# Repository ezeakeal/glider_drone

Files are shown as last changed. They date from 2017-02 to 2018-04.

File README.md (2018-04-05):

# glider_drone

A project to send a drone/glider to the stratosphere, and get it back!

## Recomendations

Setup remote debug (https://nathanpjones.com/2016/02/remote-debug-gpio-on-raspberry-pi/)

# Required hardware

1. Balloon (Hwoyee HY-1000) http://randomaerospace.com/Random_Aerospace/Balloons.html
2. Parachute (18 in. Spherachute + 42 in. Spherachute) http://spherachutes.com/
3. Glider (Go Discover FPV EPO) https://hobbyking.com/en_us/hobbykingr-tm-go-discover-fpv-plane-epo-1600mm-kit.html
4. 2 LoRa radios (http://www.hoperf.com/rf_transceiver/lora/RFM95W.html) with some interface.
5. Raspberry Pi B 2
6. Raspberry Pi servo hat + sensor hats
7. LiIon battery packs (10000 mAh recommended.. I have 2)
8. GoPro or equivalent (Xiaomi Yi is pretty great)
9. Wide angle Raspberry Pi Camera (reverse view)
10. A BUNCH of Micro SD cards + USB storage for logging and PiCamera storage 

# Prerequisites

## Setup I2C

https://learn.adafruit.com/adafruits-raspberry-pi-lesson-4-gpio-setup/configuring-i2c

## Setup Raspberry Pi interfaces

Using `raspi-config` (https://learn.sparkfun.com/tutorials/raspberry-pi-spi-and-i2c-tutorial):
1. Enable I2C
2. Enable Camera
3. Enable Remote GPIO (optional - enabling now just in case I use it later)

## Setup the disks

The glider will record video and logs to a directory specified in `glider_conf.ini`
For example, images/videos will be written to `/data/camera' by default.
Make any required directories before execution (I recommend using a USB stick)

## Setup RTIMULib

Use the following RTIMULib and guide: https://github.com/RPi-Distro/RTIMULib/tree/master/Linux
You may need to adjust the sensor ID: https://simplifyrobotics.wordpress.com/2017/05/25/mpu9250-wrong-id-error/

## Calibrate the MPU

https://github.com/RPi-Distro/RTIMULib/blob/master/Calibration.pdf

Follow all the instructions for callibration (run RTIMULibCal inside of RTEllipsoidFit)
This will generate an RTIMULib.ini config file - move that to a well-known path.
Finally, set the full path to the RTIMULib.ini file in glider_conf.ini

## Setup the Servo Hat

https://learn.adafruit.com/adafruit-16-channel-pwm-servo-hat-for-raspberry-pi/library-reference

## Find the range of your servos

The min/max duty cycle of the servo pulse can be configured in the settings.

**Note:** It took me some trial and error to figure this out (read Weird things below)

Using the PWM controller library from Adafruit or geekroo, start sending pulses to your servo.
I did the following

```
from Adafruit_PWM_Servo_Driver import PWM
import time
pwm = PWM(0x70) # i2c address for the servo hat controller
pwm.setPWMFreq(50)

# Try find min/max angle values
# pwm.setPWM(0,0, int(4096/20*(pulse_fraction)))
# I decreased the value of pulse_fraction from 1, to 0.7 until the servo stopped moving
# Then I increased the value until it stopped moving the other way
# The command is setting the pulse duration (in multiples of 1ms out of 20ms pulse)
# So pulse_fraction = 1 means 1ms@5V, then 19ms@0V

# The min I found
pwm.setPWM(0,0, int(4096/20*(0.7)))
# The max I found
pwm.setPWM(0,0, int(4096/20*(2.6)))
```

Once you have these values, set them in glider_conf.ini

### Weird things that happened

When I was trying to test the servos, some weird things happened before I found the range.

* Servo was sweeping through 30 or 40 degrees when I tried setting a new pulse width.
    * Not like a jitter or twitch, this was random sweeping for a few fractions of a second each time.
    * I thought that the servo was broken or frequency was wrong.
    * They were bad assumptions. Turns out that doubling the frequency reduced the symptom
        * Initial pulse was now reasonable in some cases!
        * But a second pulse was being sent, causing weirdness.
* Generally: if a pulse is 20ms long (50hz frequency), then:
    * 2ms high (5V) + 18ms low represents 180deg
    * 1ms high represents 0deg
* I was setting some mad values outside of this range
    * The library takes a the pulse width as a portion of 4096 (e.g. 1024 is 25% pulse width)
* **Important:** IF you give the servo a terrible value, it may not recover from trying to reach that, and future values may not work.
    * This is what led to such confusion on my part. I was putting the servo into a weird state because I lacked prior knowledge on servo pulses.

# Internal notes

## Features:
    Homesickness routine:
        If no signal from groundstation received, do not disengage from balloon
        Probably send a flag (trust of glider behaviour = True/False)
            So during flight, you flick that switch in groundstation
    Dual antennas:
        Two orientations during flight (vertical, and gliding)
        So two antennas
    IMU mounted away from electronics
    LEDs for status:
        Help Debug whats going on (issue was disk mounting this time)
    Shielded servo lines
    SMS also
    Directional tracker
    Return to sender information (like who the fuck I am)
    Better FSTAB control - must mount everytime!

## Nice to have:
    Smoke trails
    Fireworks
    Loud beeper for finding
    Groundstation application which shows where the satellites are with overlay on camera!



## Todo list:
    Fix the GPS tracking in the IMU module
        GPS tracking set the offset for the IMU, but tracking was degrees, IMU was radians

## Flight tests:
    Shake test
    Radar test (ticknock to elsewhere)
    Parachute test

newline

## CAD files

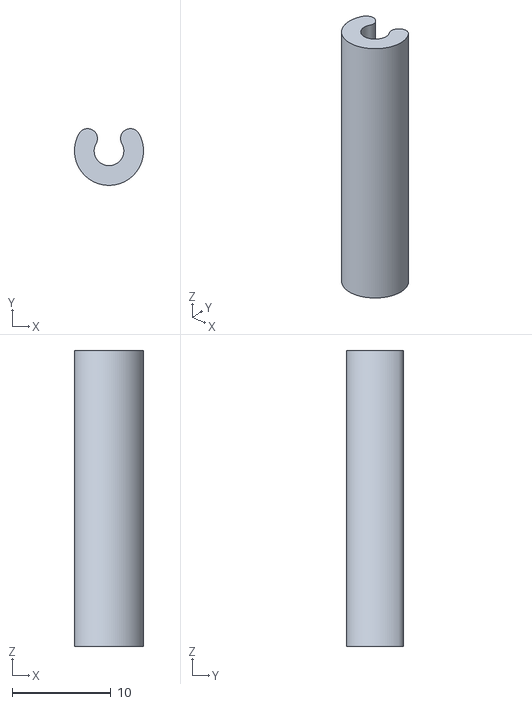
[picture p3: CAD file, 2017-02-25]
resources/3D Printed Parts/dipoleclip.stl
7.00 x 5.75 x 30.0

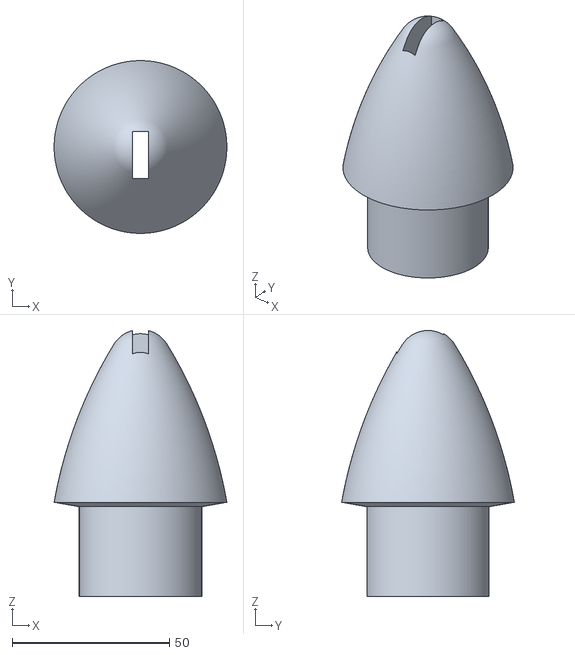
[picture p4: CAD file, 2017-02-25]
resources/3D Printed Parts/tailcone.stl
55.0 x 55.0 x 84.7

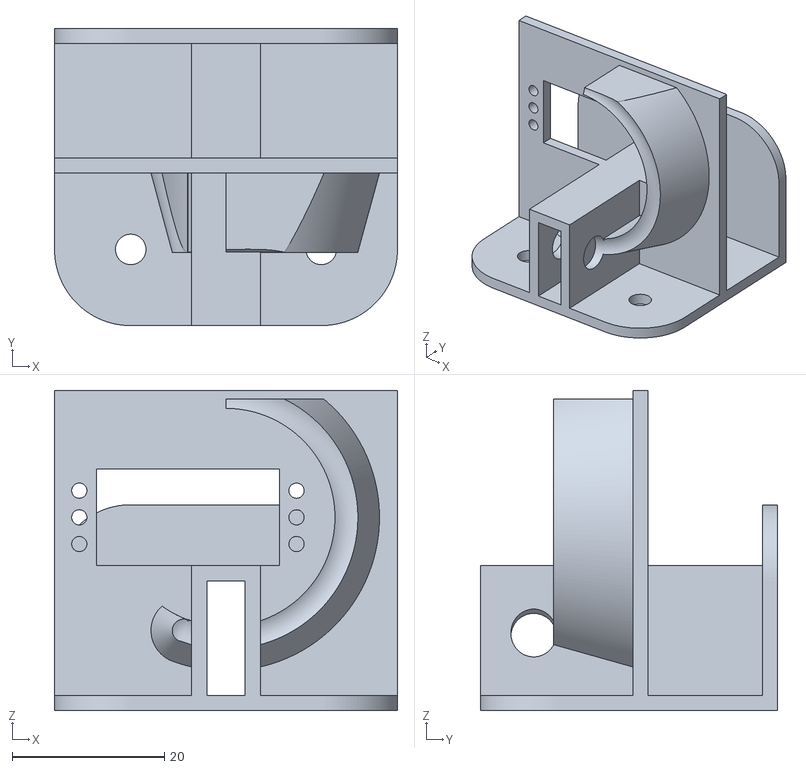
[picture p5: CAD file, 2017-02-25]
resources/3D Printed Parts/releasebracket.stl
45.0 x 39.0 x 42.0

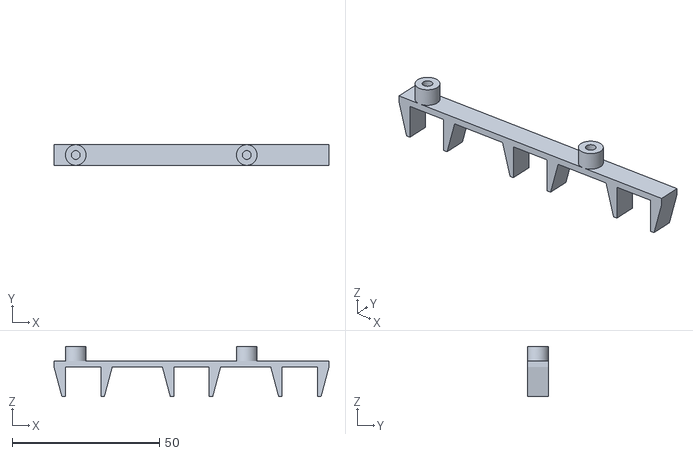
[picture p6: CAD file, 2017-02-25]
resources/3D Printed Parts/piholder.stl
93.3 x 7.00 x 17.0

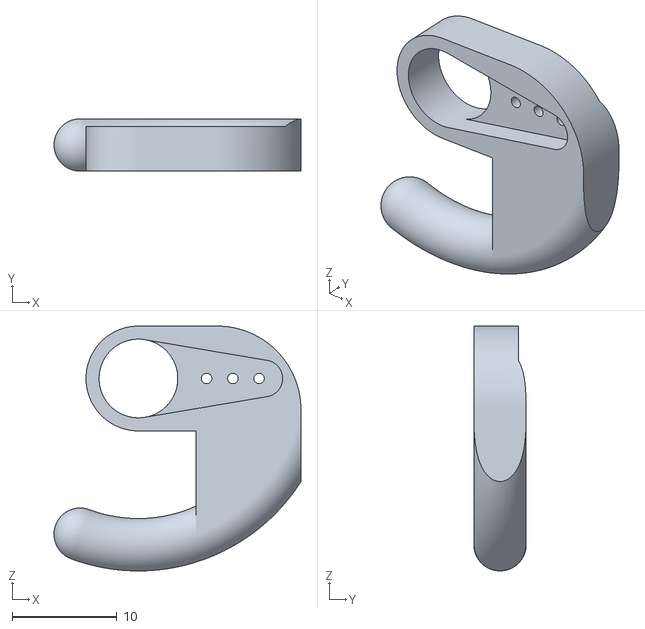
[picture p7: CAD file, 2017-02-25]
resources/3D Printed Parts/releasehook.stl
23.6 x 5.00 x 23.3

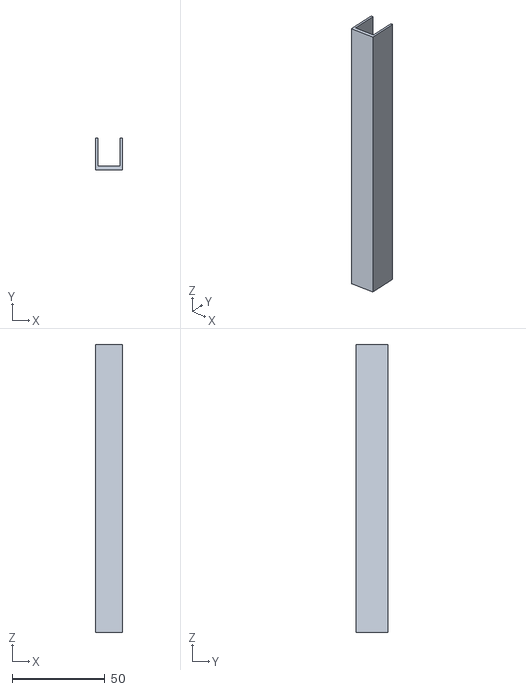
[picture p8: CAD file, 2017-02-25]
resources/3D Printed Parts/channel.stl
14.4 x 17.0 x 155.0

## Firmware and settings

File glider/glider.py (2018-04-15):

import glob
import os
import logging
import logging.config
import subprocess
import traceback

##########################################
# Configure logging
##########################################
base_dir = os.path.dirname(__file__)
conf_path = os.path.join(base_dir, "glider_conf.ini")
logging.config.fileConfig(conf_path)

LOG = logging.getLogger("glider")
logging.getLogger("Adafruit_I2C").setLevel(logging.WARN)

#########################################
# Import glider modules and states
#########################################
from modules.glider_gps import GPS
from modules.glider_camera import GliderCamera
from modules.glider_imu import IMU
from modules.glider_pilot import Pilot
from modules.glider_pwm_controller import GliderPWMController
from modules.glider_radio import GliderRadio
from modules.glider_telem import TelemetryHandler

import glider_states as gstates


##########################################
# MAIN
##########################################
class GliderCommandMixin(object):
    COMMAND_DIRECTIVES = None
    commands_received = 0
    last_command_dir = ""

    def setup_command_directives(self):
        self.COMMAND_DIRECTIVES = {
            "PA": self.pitch_change,
            "O": self.state_change,
            "TS": self.turn_severity_change,
            "DEST": self.destination_change,
            "IMAGE": self.image_command,
        }

    def command_handler(self, msg_dict, **kwargs):
        LOG.info("Handling command: %s %s" % (msg_dict, kwargs))
        command_data = str(msg_dict['message'])
        command_parts = command_data.split("|")
        command_instruction = command_parts[0]
        command_function = self.COMMAND_DIRECTIVES.get(command_instruction)
        if not command_function:
            LOG.error("No command found for instruction: %s" % command_instruction)
            return None
        try:
            self.commands_received += 1
            self.last_command_dir = command_instruction
            return command_function(command_parts)
        except:
            LOG.exception("Error in running command")
            return None

    def pitch_change(self, arg_array):
        new_pitch = float(arg_array[1])
        if 0 > new_pitch > -90:
            self.speak("Updating pitch")
            self.pilot.desired_pitch_deg = new_pitch
        else:
            LOG.error("Bad pitch (Not between 0 and -90): %s" % new_pitch)

    def state_change(self, arg_array):
        new_state = arg_array[1]
        if new_state in self.state_machine.keys():
            self.speak("Updating state: %s" % new_state)
            self.current_state = new_state
        else:
            LOG.error("Bad state requested: %s" % new_state)

    def turn_severity_change(self, arg_array):
        new_severity = float(arg_array[1])
        if 0 < new_severity < 3:
            self.speak("Updating severity")
            self.pilot.turn_severity = new_severity
        else:
            LOG.error("Bad severity (Not between 0 and 3): %s" % new_severity)

    def destination_change(self, arg_array):
        lat = arg_array[1]
        lon = arg_array[2]
        self.speak("Updating destination")
        self.pilot.update_destination(lat, lon)

    def image_command(self, arg_array):
        self.speak("Sending image")
        newest_image = max(glob.iglob('%s/low_*.jpg' % self.camera.photo_path), key=os.path.getctime)
        self.radio.sendImage(newest_image)


class Glider(GliderCommandMixin):
    state_machine = {
        "PACKAGING": gstates.packaging(),
        "HEALTH_CHECK": gstates.healthCheck(),
        "ASCENT": gstates.ascent(),
        "RELEASE": gstates.release(),
        "FLIGHT": gstates.glide(),
        "PARACHUTE": gstates.parachute(),
        "RECOVER": gstates.recovery(),
        "ERROR": gstates.errorState(),

        "TEST_CHUTE": gstates.test_chute(),
        "TEST_RELEASE": gstates.test_release(),
    }
    current_state = "FLIGHT"

    def __init__(self):
        # Initialize all modules
        self.speak("Initializing")
        self.gps = GPS()
        self.imu = IMU()
        self.radio = GliderRadio(self.command_handler)
        self.camera = GliderCamera()
        self.pwm_controller = GliderPWMController()
        # The pilot and telemetry handler need access to the instances we created
        self.pilot = Pilot(self.imu)
        self.telemetry_handler = TelemetryHandler(self.radio, self.imu, self.pilot, self.gps, self)
        self.start_modules()
        self.setup_command_directives()
        self.speak("IKAHRO ready")

    def start_modules(self):
        # Start up modules
        self.speak("Starting modules")
        self.gps.start()
        self.radio.start()
        self.camera.start()
        self.telemetry_handler.start()
        self.pwm_controller.start()

    def stop_modules(self):
        self.speak("Stopping modules")
        self.gps.stop()
        self.radio.stop()
        self.camera.stop()
        self.telemetry_handler.stop()
        self.pwm_controller.stop()

    def stop(self):
        self.speak("Shutting down")
        self.stop_modules()

    def speak(self, text):
        LOG.info("Speaking %s" % text)
        with open(os.devnull, "w") as f:
            subprocess.Popen(["espeak", "-ven-us", "-m", "-p", "70", "-s", "180", text], stdout=f, stderr=f)

    def run_state_machine(self):
        self.running = True
        while self.running:
            try:
                LOG.debug("Current state: %s" % self.current_state)
                stateClass = self.state_machine[self.current_state]
                stateClass.rest()
                stateClass.execute(self)

                # Check if we switch
                newState = stateClass.switch()
                LOG.debug("New state: %s" % newState)

                # Switch in to new state
                if newState:
                    LOG.debug("State is changing from (%s) to (%s)" % (
                        self.current_state, newState))
                    self.speak("Switching state to %s" % newState)
                    self.current_state = newState

            except KeyboardInterrupt:
                self.stop()
                raise # Don't go to error state, close the program!
            except:
                LOG.exception("Error in Glider state machine")
                self.current_state = "ERROR"


if __name__ == '__main__':
    try:
        glider = Glider()
        glider.run_state_machine()
        glider.stop()
    except Exception as e:
        print traceback.print_exc()
        with open(os.devnull, "w") as devnull:
            subprocess.call(
                ["espeak", "-ven+f3", "-m", "-p", "70", "-s", "180", "Error encountered! %s" % str(e)],
                stdout=devnull, stderr=devnull
            )

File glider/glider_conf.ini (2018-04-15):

[loggers]
keys=root

[handlers]
keys=stream,file

[formatters]
keys=formatter

[logger_root]
level=WARN
handlers=stream,file

[handler_stream]
class=StreamHandler
level=DEBUG
formatter=formatter
args=(sys.stderr,)

[handler_file]
class=handlers.TimedRotatingFileHandler
interval=midnight
backupCount=5
formatter=formatter
level=WARN
args=('/tmp/glider.log',)

[formatter_formatter]
format=%(asctime)s %(name)-12s L.%(lineno)d %(levelname)-8s %(message)s

[redis_client]
host=127.0.0.1
port=6379
db=0

[gps]
fake_location=/tmp/location.json

[camera]
data_dir=/data/camera

[imu]
# Remove the .ini extension (https://github.com/Nick-Currawong/RTIMULib2/tree/master/Linux/python#usage)
conf_path=/home/pi/imu_conf/RTIMULib
# Max allowed difference from IMU heading and GPS heading in degrees before IMU is corrected by offset
heading_discrepancy_allowance=5.0

[servo]
# servo hat i2c address
hat_i2c_address=0x70
# the offset for servo pulse in ms
pulse_lag_ms=100
# Servo addresses
flap_address_left_near=1
flap_address_right_near=0
flap_address_left_far=2
flap_address_right_far=3
flap_address_rear=6
flap_address_rudder=7

servo_address_release=10
servo_address_parachute=11
servo_center_release=90
servo_center_parachute=90

# Servo frequency
frequency=50
# min/max pulse width for servos
min_ms=0.7
max_ms=2.4
# seconds between servo commands
controller_breather=0.02

[telemetry]
interval_data = 1
interval_telem = 5

[radio]
port = /dev/ttyAMA0
baud_rate = 38400
callsign = glider
groundstation_address = 0xFF
address = 0xAA

[flight]
# This is the desired pitch of the glider in degrees
# We want it to generally point down to keep flying
nominal_pitch_deg = -10
# Turn severity defines how much the glider will roll
# proportional to the difference in desired direction
# This multiplies the apparent difference in angle, as
# tan will ramp up to +/- infinity at either +/- 90deg
# This gets limited later
turn_severity = 1.0
# The most the servos can move in degrees (either way, e.g. 20 = centre +- 20)
servo_range = 45
# Initial GPS coordinates to target
initial_destination = 54.673146,-7.490621
# How often to update the wings
wing_update_interval = 0.01
# Store the angle (degrees) which makes the wings centered/flat
flap_range_left_near= 55,115
flap_range_left_far = 55,115
flap_range_right_near= 50,110
flap_range_right_far = 138,78
flap_range_rudder = 112,12
flap_range_rear = 170,90
heading_discrepancy_allowance = 5

# Whether to use the near/far flaps on the wings
use_near_wing_flaps = True
use_far_wing_flaps = True
# How often to update the glider location in seconds (updates the desired bearing)
location_refresh_interval=15
# Critical ground speed (m/s) - Values less or equal to this result in a -45 degree dive
# The pitch angle will decrease in severity proportional to sin(0) -> sin(pi/2). Generally 45 degrees and then chills
# Nominal ground speed is where the glider should stop pitching to gather speed
pitch_critical_ground_speed = 13
pitch_nominal_ground_speed = 30

[mission]
# When to let go of the balloon
balloon_release_altitude = 11000
wing_antifreeze_wiggle_altitude = 10000
# When to deploy the parachute
parachute_height = -2000
# How many seconds to wait before releasing the chute
dive_time_before_chute = 5
# Contact detail to say when waiting for rescue
contact_detail = "Daniel at +353 83 345 7414"
# Alarm Siren
siren_duration = 1
siren_pin = 18

[test_chute]
chute_delay_time = 10

[test_release]
release_delay_time = 5

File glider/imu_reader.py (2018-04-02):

import sys

sys.path.append('.')
import RTIMU
import os.path
import time
import redis

from config import glider_config
SETTINGS_FILE = glider_config.get("imu", "conf_path")

print("Using settings file " + SETTINGS_FILE + ".ini")
if not os.path.exists(SETTINGS_FILE + ".ini"):
  print("Settings file does not exist, will be created")

s = RTIMU.Settings(SETTINGS_FILE)
imu = RTIMU.RTIMU(s)

print("IMU Name: " + imu.IMUName())

if (not imu.IMUInit()):
    print("IMU Init Failed")
    sys.exit(1)
else:
    print("IMU Init Succeeded")

redis_client = redis.StrictRedis(
    host=glider_config.get("redis_client", "host"),
    port=glider_config.get("redis_client", "port"),
    db=glider_config.get("redis_client", "db")
)

# this is a good time to set any fusion parameters
imu.setSlerpPower(0.02)
imu.setGyroEnable(True)
imu.setAccelEnable(True)
imu.setCompassEnable(True)

poll_interval = imu.IMUGetPollInterval()

print("Recommended Poll Interval: %dmS\n" % poll_interval)
while True:
  if imu.IMURead():
    r,p,y = imu.getFusionData()
    redis_client.set("roll", r)
    redis_client.set("pitch", p)
    redis_client.set("yaw", y)

    time.sleep(poll_interval*1.0/1000.0)

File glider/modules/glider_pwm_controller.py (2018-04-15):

import math
import time
import logging
# noinspection PyUnresolvedReferences
import Adafruit_PCA9685
from threading import Thread
from . import glider_config

LOG = logging.getLogger("glider.%s" % __name__)


class GliderPWMController(object):
    """
    Threaded PWM controller.
    Although the microcontroller is managing the servo angles in its own time,
    if we write too many angles to the servos at once, they all go nuts!
    So instead we will set desired angle, and a thread will iterate over
    and update all servo angles in sequence with some delay.
    """

    threadAlive = False

    address = glider_config.get("servo", "hat_i2c_address")
    frequency = glider_config.getint("servo", "frequency")
    servo_pulse_lag = glider_config.getint("servo", "pulse_lag_ms")
    controller_breather = glider_config.getfloat("servo", "controller_breather")

    servo_min_ms = glider_config.getfloat("servo", "min_ms")
    servo_max_ms = glider_config.getfloat("servo", "max_ms")

    # We COULD lump this in with flap_addresses and angles, but I don't want code to ever accidentally trigger a release
    servo_addresses = {"parachute": None, "release": None}
    servo_angles = {"parachute": None, "release": None}

    flap_addresses = {'rudder': None, 'rear': None,
                       'left_near': None, 'right_near': None,
                       'left_far': None, 'right_far': None}

    flap_angles = {'rudder': None, 'rear': None,
                    'left_near': None, 'right_near': None,
                    'left_far': None, 'right_far': None}

    flap_ranges = {'rudder': None, 'rear': None,
                    'left_near': None, 'right_near': None,
                    'left_far': None, 'right_far': None}

    _current_flap_angles = {} # Used to maintain the current angle and reduce calls to the PWM controller (unused)

    def __init__(self):
        LOG.debug("Staring up PWM Controller (Address=%s Frequency=%shz)" % (self.address, self.frequency))
        self.pwm = Adafruit_PCA9685.PCA9685(address=int(self.address, 16))
        self.pwm.set_pwm_freq(self.frequency)
        self._read_flap_config()
        self.start()

    def _read_flap_config(self):
        for flap in self.flap_addresses.keys():
            self.flap_addresses[flap] = glider_config.getint("servo", "flap_address_%s" % flap)
            flap_angle_range = [float(x) for x in glider_config.get("flight", "flap_range_%s" % flap).split(",")]
            self.flap_ranges[flap] = flap_angle_range
            self.flap_angles[flap] = sum(flap_angle_range)/2
        for servo in self.servo_addresses.keys():
            self.servo_addresses[servo] = glider_config.getint("servo", "servo_address_%s" % servo)
            self.servo_angles[servo] = glider_config.getfloat("servo", "servo_center_%s" % servo)

    def start(self):
        servo_update_thread = Thread( target=self.update_servo_angles, args=() )
        self.threadAlive = True
        LOG.info("Setting initial servo position")
        self.servo_init_position()
        LOG.info("Starting up Servo Controller thread now")
        servo_update_thread.start()

    def servo_init_position(self, delay=0.5):
        for flap, address in self.flap_addresses.items():
            center_angle = self.flap_angles[flap]
            self._set_servo_angle(address, center_angle , self.servo_min_ms, self.servo_max_ms, force=True)
            time.sleep(delay)

    def stop(self):
        self.servo_init_position(delay=0.1)
        time.sleep(1)
        self.threadAlive = False

    def update_servo_angles(self):
        while self.threadAlive:
            for flap_id, angle in self.flap_angles.items():
                servo_address = self.flap_addresses[flap_id]
                self._set_servo_angle(servo_address, angle, flap_id=flap_id)
            for servo_id, angle in self.servo_angles.items():
                servo_address = self.servo_addresses[servo_id]
                self._set_servo_angle(servo_address, angle, servo_id=servo_id)
            time.sleep(self.controller_breather) # Sleep at least this much - can happen if there are no angle updates

    def _set_servo_angle(self, servo_address, angle, min_ms=None, max_ms=None, force=True, flap_id=None, servo_id=None):
        if not min_ms:
            min_ms = self.servo_min_ms
        if not max_ms:
            max_ms = self.servo_max_ms

        angle = math.ceil(angle)  # round the angle to reduce calls for minor adjustments
        # if not force:
        #     if flap_id and angle == self.flap_angles[flap_id]:
        #         return
        #     if servo_id and angle == self.servo_angles[servo_id]:
        #         return

        ms_range = float(max_ms - min_ms)
        LOG.debug("Servo pulse ms range: %s" % ms_range)
        # This is the pulse we add to the initial pulse of 1ms to change the angle
        # e.g. 1ms = 0deg, 2ms = 180deg, so angle_pulse of 0.5 results in 1.5 = 90deg
        angle_pulse = (angle/180.0 * ms_range)
        LOG.debug("Angle fraction (%s = %s)" % (angle, angle_pulse))
        pulse_width = int(4096/(1000/self.frequency)*(min_ms + angle_pulse))
        LOG.debug("Setting servo(%s) pulse (fraction=%s duration=%sms)" % (
            servo_address, min_ms+angle_pulse, pulse_width))
        self.pwm.set_pwm(servo_address, self.servo_pulse_lag, pulse_width + self.servo_pulse_lag)
        time.sleep(self.controller_breather)

    # def set_flap_angles(self, angle_dictionary):
    #     LOG.debug("Setting flaps: %s" % (angle_dictionary))
    #     self.flap_angles.update(angle_dictionary)

    def set_flap_scales(self, scale_angle_dictionary):
        # Used to take in a range between 0 and 1 and set the angle accordingly between the servo min/max
        # 0.5 would be center flap for neutral
        LOG.debug("Setting flap scales: %s" % (scale_angle_dictionary))
        for flap, scale in scale_angle_dictionary.items():
            angle_range = self.flap_ranges[flap]
            scaled_angle = angle_range[0] + scale*(angle_range[1]-angle_range[0])
            self.flap_angles[flap] = scaled_angle

    def release_parachute(self, reset=False):
        LOG.debug("Releasing parachute")
        angle_parachute = 180 if reset else 0
        self.servo_angles['parachute'] = angle_parachute

    def release_from_balloon(self, reset=False):
        LOG.debug("Releasing from balloon")
        angle_balloon_release = 10 if reset else 180
        self.servo_angles['release'] = angle_balloon_release

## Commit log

2017-02-25 Initial commit of some rescued code from previous glider
    [channel.stl, dipoleclip.stl, piholder.stl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]
2017-07-12 Updated servo controller and debugging tools
2017-07-13 Updating logging and general bugfixing from old codebase. Things are almost working
    [glider.py, glider_camera.py, glider_conf.ini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]
2017-07-13 The software now works! Have to optimize and build it into the glider, then add sensors and LEDs
2017-07-22 Updated and groundstation is working quite well
2017-07-30 The init() method of sat_radio calls start(). I had followed the convention of my own code and called start() explicitly, which led to 2 connections to serial port fighting for info
2017-08-10 Updated glider code to use GPS track as a continuous correction of the IMU compass - which can be altered by weak magnetic fields... like servo motors
    [glider.py, glider_camera.py, glider_conf.ini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]
2018-04-02 Significant update of local changes as well as the updates for a new testing class that will demonstrate the pilot functionality, and the code updates for a new glider frame (Sky Eye) to be used. The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
    [channel.stl, dipoleclip.stl, piholder.stl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]
2018-04-03 Updated wing controller and pilot unit test to work with Sky Eye drone - configured config for default servo hookups
2018-04-15 Updated code with better testing and removed some unnecessary threading
